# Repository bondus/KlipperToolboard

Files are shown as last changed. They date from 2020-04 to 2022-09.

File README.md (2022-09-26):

# Huvud 3D Printer toolhead board
A very small 3D printer board for use on a direct drive toolhead. It is designed to be used with Klipper firmware.
Klipper has the awesome feature to be able to use multiple MCUs connected to the host over a (relatively) high latency connection. Using CAN bus it is possible to chain many boards using just a pair of twisted wires and power. A good solution for multiple head 3D printers.

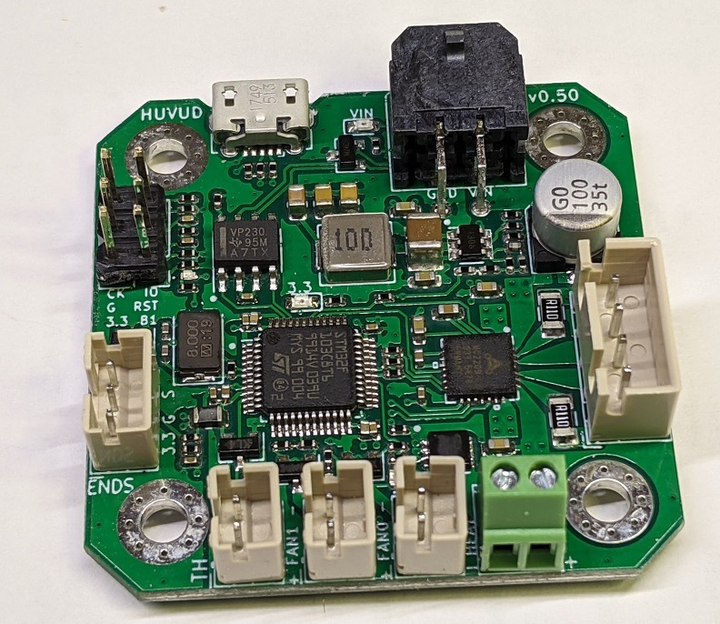
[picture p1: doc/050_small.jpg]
Image of Board


Features: 
* CAN bus. 
* One TMC2209 stepper driver for the extruder
* Two MOSFETs for fans
* One big MOSFET for the hotend heater
* Thermistor input
* Support for an endstop (or filament runout sensnor)
* STM32F103 72Mhz 32bit ARM MCU
* USB, for flashing firmware

Main power is 12-24V. 24V is preferred to keep the currents low

All done in KiCad and open source. 

If you are interesting in helping out, testing or eventually using this board feel free to contact me at glpontus@gmail.com.

### Documentation

* [Pinout and hook up](doc/pinout.md)
* [Klipper configuration](doc/klipper.md)
* [CAN bus](doc/canbus.md)
* [Prototype versions of the board](doc/versions.md)

---
Buy it at:

* Lukes Lab: https://lukeslabonline.com/products/huvud
* Tindie: https://www.tindie.com/products/huvud/huvud-3d-printer-hotend-control-board/

---

Read more about the project activites over at hackaday:
https://hackaday.io/project/174429-huvud-a-3d-printer-tool-head-controller-board

---

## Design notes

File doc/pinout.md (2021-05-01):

# Huvud Hardware, Pinout and Hookup

(all pictures are of pre production partially hand assembled boards, the real thing will be slighly different and look a lot better)

## Pinout 

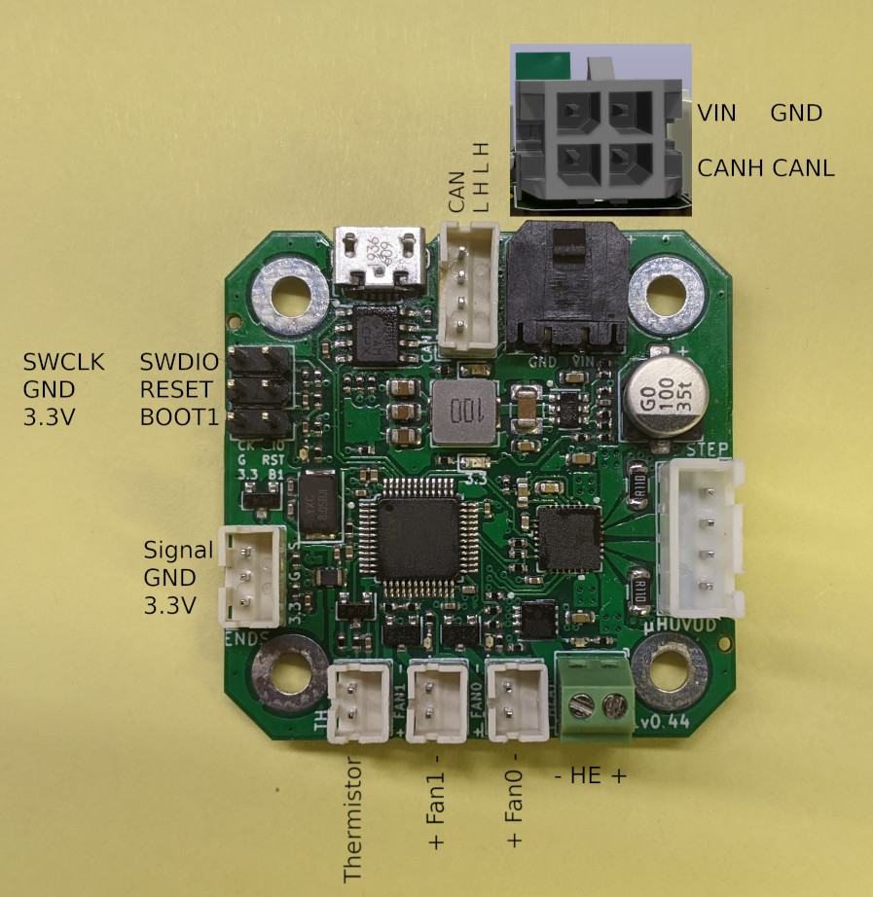
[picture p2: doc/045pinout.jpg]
Pinout


Function         | Pin  | Comment
-----------------|------|---------
Stepper EN       | PB6  |
Stepper STEP     | PB3  |
Stepper DIR      | PB4  |
Stepper DIAG     | PB5  |
Stepper Uart RX  | PA10 |
Stepper Uart TX  | PA9  |
CAN RX           | PB8  |
CAN TX           | PB9  |
USB +            | PA12 |
USB -            | PA11 |
FAN0             | PA8  |
FAN1             | PA7  |
Heater           | PA6  | 
Endstop          | PA1  | 10k pull up
Thermistor       | PA0  | 2.2k Pull Up
LED              | PC13 | Blue LED by the debug connector
Crystal 8Mhz     | PD0/PD1 |
BOOT1            | PB2  | 10k pull down
SWDIO            | PA13 | 10k pull down
SWDCLK           | PA14 | 10k pull down

Look at [printer.cfg](printer.cfg) for an example configuration.

## Powering

The board works from 10V up to 28V. It must be powered through the Molex Micro-Fit connector. It can not be powered with USB and powering though the 3.3V must be avoided, the stepper driver can get damaged.

The power connector is rated for max 8A

## Hooking up peripherals

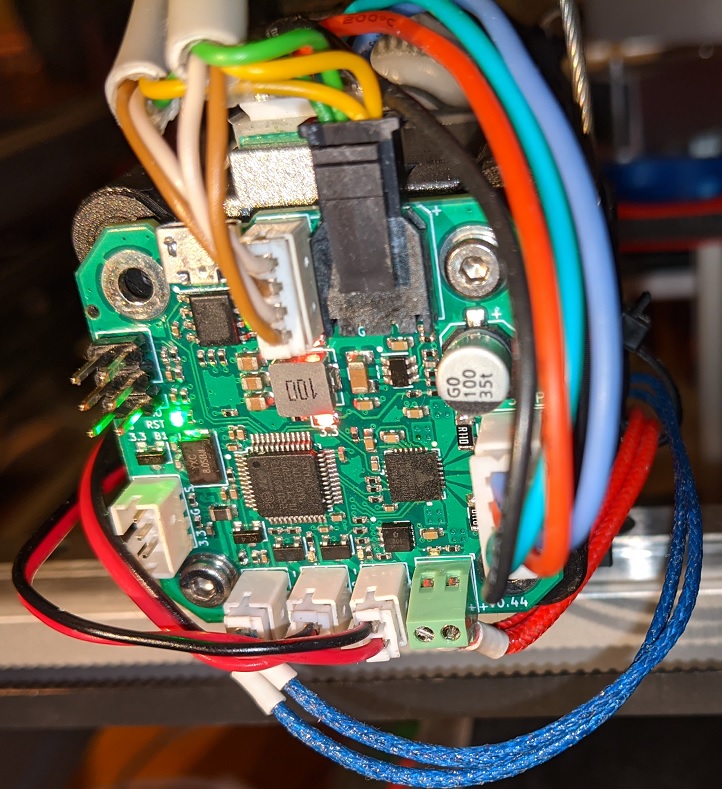
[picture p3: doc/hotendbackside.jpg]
Huvud on hotend


### Fans

JST-PH 2 mm connectors. Max 1A per fan

### Thermistor / PT1000

JST-PH 2 mm connectors. The thermistor input has a 2.2KOhm pullup resistor to allow for better resolution when using a PT1000 sensor.

### Hotend heater

Max 4A. Enough for a 100W heater when running on 24V

### Endstop

The endstop supplies 3.3V to work with an optical endstop sensors. For a microswitch (NO) connect it to GND and Signal.
Please note that klipper at the moment requires an endstop to be on the same board as the stepper driver. If the board is used for an extruder the endstop can not be used for a bed probe. The endstop can be used as a filament runout on a hotend, or as an axis endstop if the board is used for movement.

### CAN bus

Power and CAN bus in in the same Molex MicroFit connector.
There is no on board CAN bus termination resistor.

### LED

There is a user controlled green LED near the debug connector, it is connected to PC13. It is normally on while klipper is running. It's also used by the HID bootloader to signal various states.

## Thermals

The TMC2209 is a very efficient stepper driver and does not generate a large mount of heat. Still temerature should be checked if you run at high currents. The board is designed to spread the heat over the entire PCB. 

Testing shows that the board works comfortly without any extra cooling up to 1.2A driver current (it will reach about 25C above ambient). The board is designed to work up to 85C, so even if it gets very hot it will work fine. 

If the driver or boards gets too hot add small cooling fins, or if possible use a thick thermal pad on the bottom to lead the heat into something like an alu extrusion or other metal object.

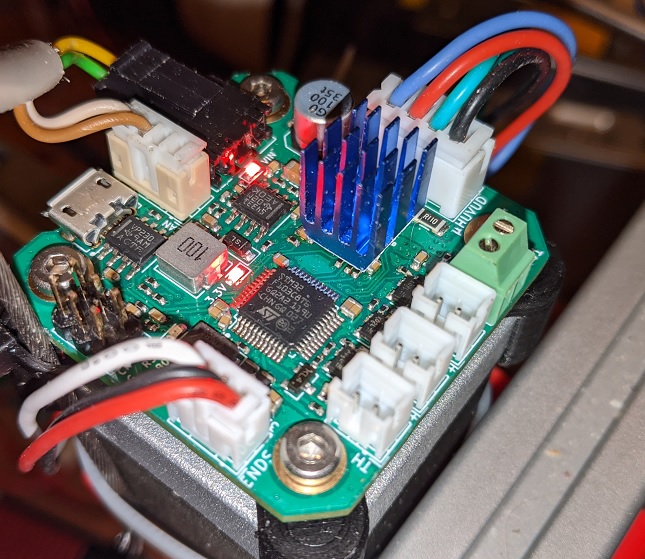
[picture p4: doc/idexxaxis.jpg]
IDEX x axis with cooling fins


If huvud is used for movement you can even monitor the temperature with a thermistor and turn on a fan if it gets too hot.

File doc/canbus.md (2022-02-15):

# Working with CAN bus

## Adapters

You will need a CAN bus adapter for your Raspberry Pi (or other board you run klippy on). There are many options available.

The adapter must support Linux socketcan

### USB CAN adapter

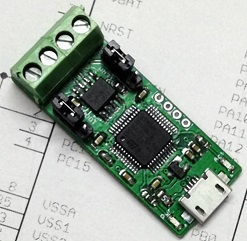
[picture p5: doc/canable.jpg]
Canable USB CAN clone


There is a very good open source firmware for STM32 based USB adapters, https://github.com/candle-usb/candleLight_fw. Any board running this firmware should work fine. There are plenty of open source hardware alteratives that runs this firmware.

Get one at https://openlightlabs.com/products/canable-0-4 or find a clone on aliexpress.

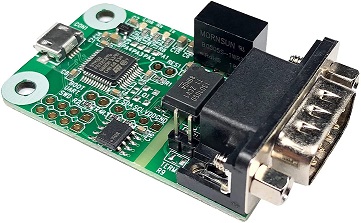
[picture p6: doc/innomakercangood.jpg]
Innomaker CAN USB


Innomaker has an USB CAN bus adapter widely available. It had a firmware bug that was reported and fixed March 2020, newer boards should have this fixed. 

### MCP2515 based CAN HATs

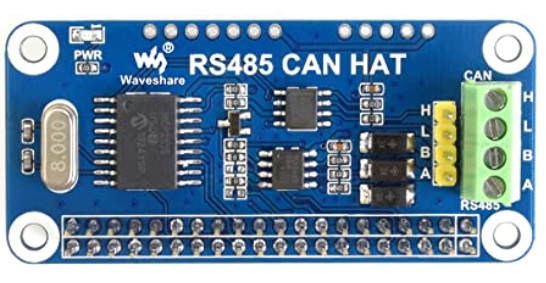
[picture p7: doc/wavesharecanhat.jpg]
Waveshare CAN HAT


The MCP2515 is a very common SPI connected CAN bus chip. It is a pretty bad options since it has very small buffers on chip and creates a lot of CPU load on the Raspberry Pi, and has a tendency to drop packet. It is not recomended if you use more than 1 or 2 boards or if you plan to use the accelerometer.

You have to run the CAN bus at 250kbits/s or possibly 500kbits/s. An older Pi, or a Pi Zero will not work reliably, it has to be a Pi3 or Pi4 or better.

An easily available option is "Waveshare RS485 CAN HAT"

TBD: Is the MCP2517/MCP2518 based HATs any better? They are made for CAN-fd but are backwards compatible. As the drivers are not in the mainline kernel it's non-trivial to get an MCP2517/8 to work. 

## Linux and Klipper setup

Please read https://github.com/KevinOConnor/klipper/blob/master/docs/CANBUS.md

## Wiring

### Cables

CAN bus is a bus, it must be terminated at each end with 120ohm resistors.

Twisted pair ... Ethernet cables or specifically made CAN bus cables. If shielding is used it should only be grounded at one point.

As we run default at 500kbits/s each stub length can be up to 1.6m long.

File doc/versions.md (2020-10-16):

# Versions of the Huvud Toolboard

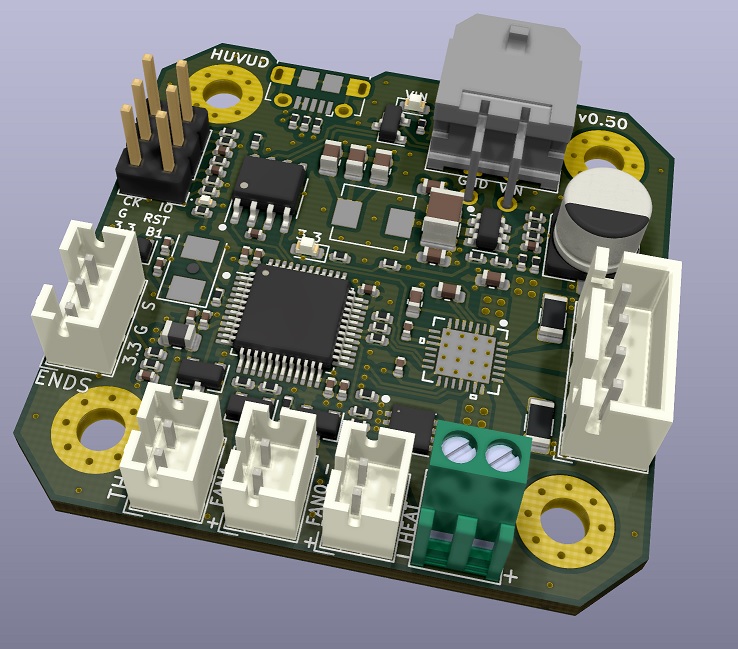
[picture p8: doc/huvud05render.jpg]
Render of Huvud v.050


## 0.50

Volume production about to start

+ Changed the power connector from a 2x1 Molex Micro-fit to a 2x2. The 2 extra pins are used for CAN bus. Allows one single connector back to klippy.
* Removed the 4 pin CAN connector
* Added ESD protection on the CAN bus
+ Test pads on the bottom for production testing

# Prototypes

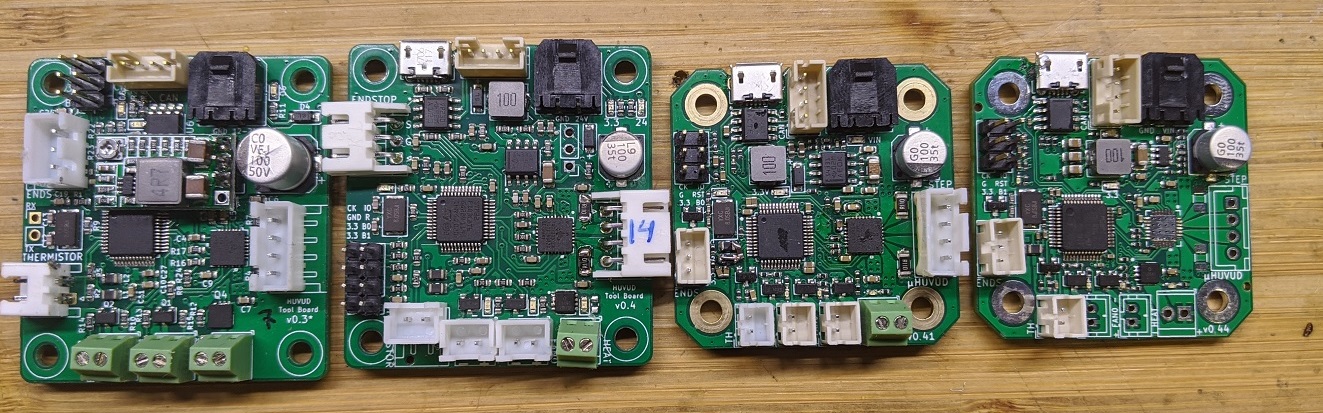
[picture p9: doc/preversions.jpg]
Pre production version


## 0.3

First Version

* 4.7k thermistor pullup
* 0.100ohm sense resistor for the TMC2209
+ It works!!!
- External 3.3V voltage regulator
- No USB, has to be flashed with an ST-LINK
- Very noisy thermistor signal (only seen when measuring, still works good in klipper)
* No SMDs smaller than 0603

## 0.4

+ USB
+ On board 3.3V voltage regulator 
+ 110ohm sense resistor

## 0.41

* 2.2k thermistor pullup to allow the use of PT1000 temperature proble
* Smaller size. 42x42 mm with 31x31 mm screw pattern, matches NEMA 17.
* Most small SMDs are 0402
* Most connectors changed to JST-PH 2.0 mm
* ESD protection on endstop and thermistor
- Weak heater MOSFET (max 4A with no margins at all)
- Forgot the pins for BOOT1, it's not possible to enter the bootloader

## 0.44

+ Greatly reduced ripple on 3.3V by redesigning and changing to a different voltage regulator IC
+ Greatly reduced thermistor noise, proper filtering of VREF

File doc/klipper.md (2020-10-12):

## Klipper configuration

### Firmware configuration

* Enable Micro-controller Architecture (STMicroelectronics STM32)
* Pick STM32F103
* Pick Bootloader offset (2KiB bootloader (HID Bootloader))
* Disable Use USB for communication (instead of serial)
* Enable Use CAN for communication (instead of seria)l
* Pick CAN pins (Pins PB8(rx) and PB9(tx))

It is possible to use USB instead of the CAN bus, like most other controller boards. 

### Bootloader and Flashing

The boards come preloaded with the HID bootloader for flashing over USB. Note that the board can not be powered over USB. 

To enter the bootloader pin BOOT1 must be connected to 3.3V when the board is powered up or reset. When in the bootloader the green LED will flash quickly. Flash with the command "make flash FLASH_DEVICE=1209:beba"

Hopefully a CAN capable bootloader will be developed to allow flashing over CAN bus.

### printer.cfg

[Example partial printer.cfg](printer.cfg)

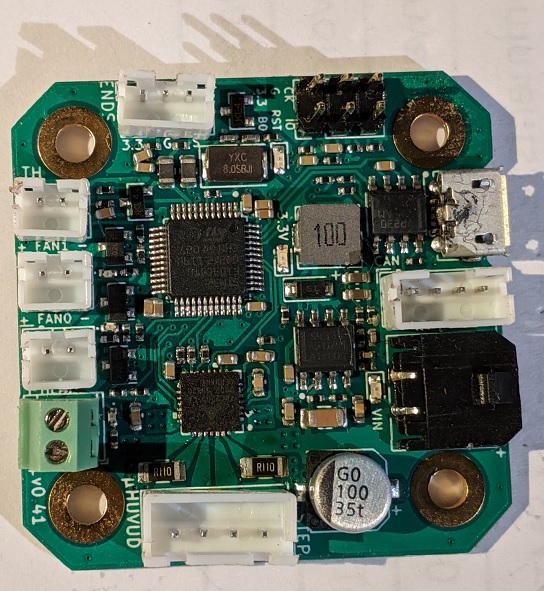
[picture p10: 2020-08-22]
doc/uHuvud0.41.jpg

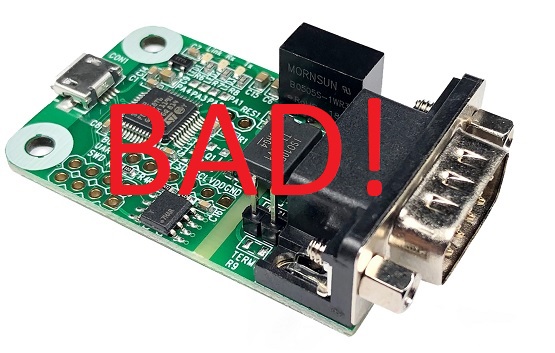
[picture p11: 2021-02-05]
doc/innomakerusbcan.jpg

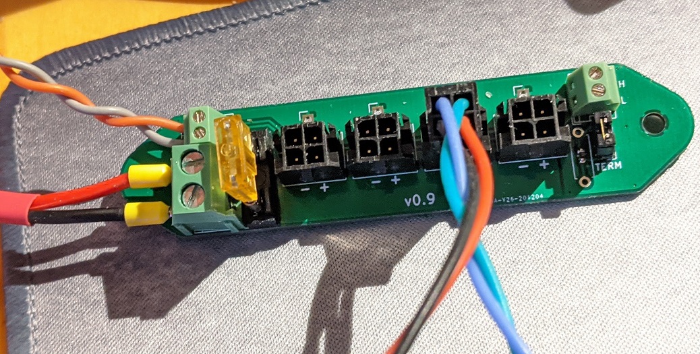
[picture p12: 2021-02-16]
doc/PowerCanDist.jpg

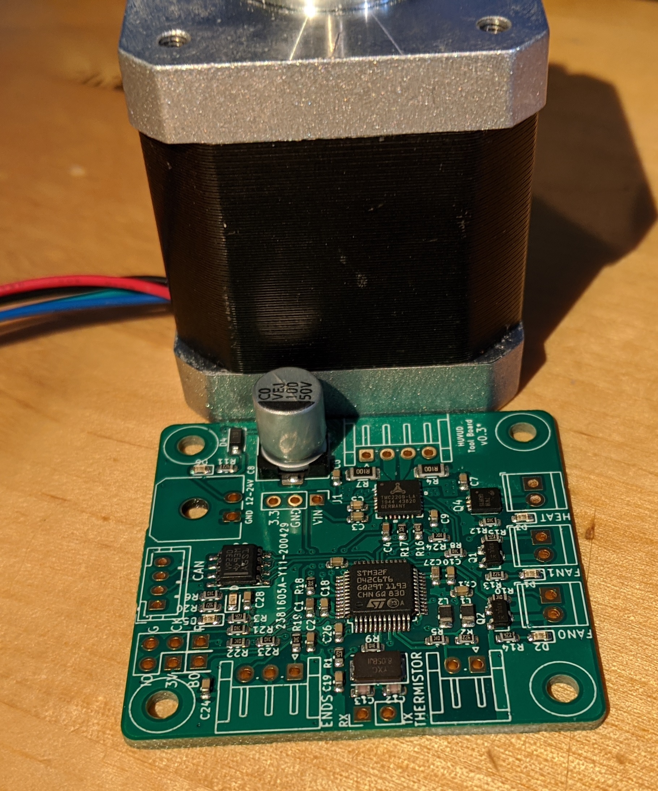
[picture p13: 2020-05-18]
FirstPic.jpg

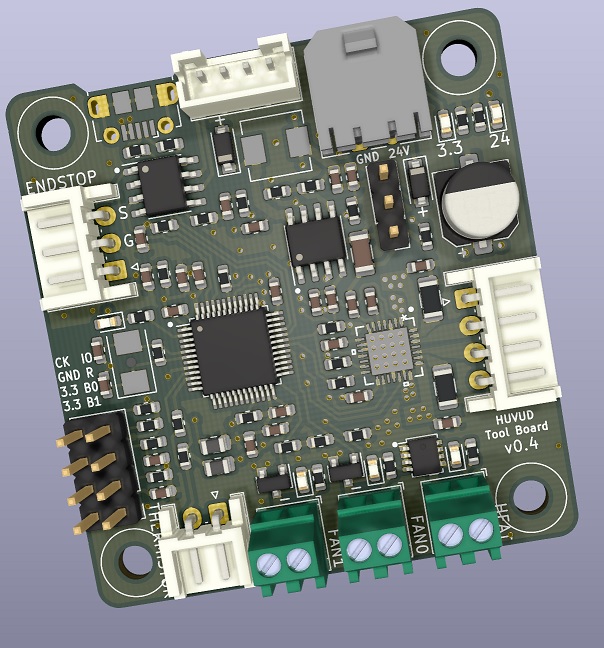
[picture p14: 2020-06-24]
doc/Huvud0.4Render.jpg

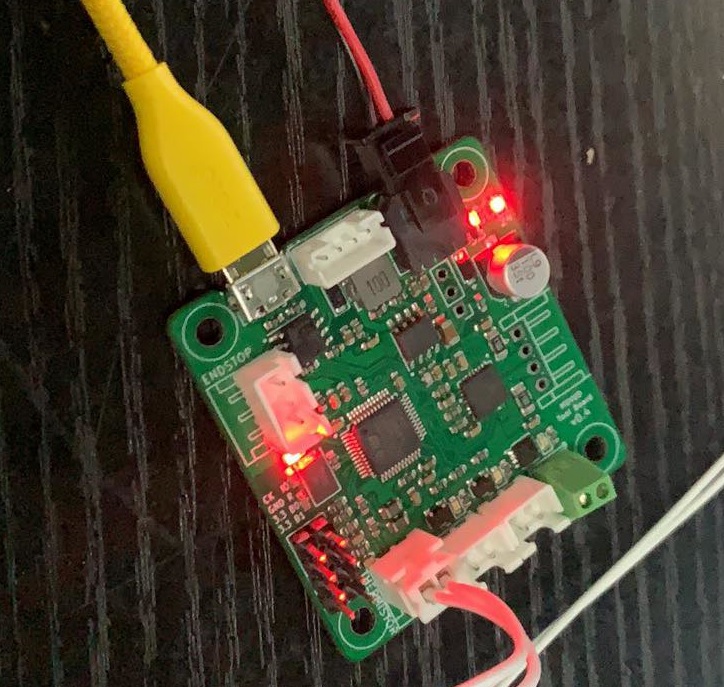
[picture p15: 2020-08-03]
doc/Huvud0.4Real.jpg

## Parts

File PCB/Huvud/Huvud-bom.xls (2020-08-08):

Item # | Designator | Qty | Manufacturer | Part Nr | Value | Package | Type | Notes | LCSC Part #（optional）
1 | C11,C10,C17,C18,C19,C26,C28,C2,C24,C21 | 10 |  |  | 0.1uF | 0603 | SMD |  | C14663
2 | C12,C13 | 2 |  |  | 22pF | 0603 | SMD |  | C1653
3 | C14 | 1 |  |  | 2.2nF | 0603 | SMD |  | C1604
4 | C15 | 1 |  |  | 15pF | 0603 | SMD |  | C1644
5 | C16 | 1 |  |  | 10nF | 0603 | SMD |  | C57112
6 | C20 | 1 |  |  | 10uF | 1206 | SMD |  | C13585
7 | C22,C23 | 2 |  |  | 10uF | 0603 | SMD |  | C19702
8 | C4,C1,C27 | 3 |  |  | 4.7uF | 0603 | SMD |  | C19666
9 | C5 | 1 |  |  | 22nf/50V | 0603 | SMD | Min 35V | C21122
10 | C8 | 1 | Lelon | VZT101M1VTR-0606 | 100uF/35V | CP_Elec 6.3x5.8 | SMD | Min 35V | C249982
11 | C9,C6,C7,C3 | 4 |  |  | 100nF/50V | 0603 | SMD | Min 35V | C14663
12 | D1,D3,D2 | 3 |  |  | LED Green | 0603 | SMD |  | C72043
13 | D4,D7 | 2 | Changjiang Electronics Tech | B5819W | B5819W | SOD-123 | SMD |  | C8598
14 | D6,D8,D5 | 3 |  |  | LED Red | 0603 | SMD |  | C2286
15 | J12 | 1 | Molex | 105017-0001 | USB_Micro-B_Molex-105017-0001 | USB_Micro-B_Molex-105017-0001 | SMD |  | C10418
16 | L1,L2 | 2 |  |  | 22uH | 0805 | SMD |  | C32375
17 | L3 | 1 | Sunlord (or similar) | MWSA0503-100MT | 10uH | 5.2x5.4x3.0mm | SMD |  | C139506
18 | Q2,Q1 | 2 | Alpha & Omega Semicon (or similar) | AO3400A | AO3400A | SOT-23 | SMD |  | C20917
19 | Q4 | 1 | Shenzhen ruichips Semicon | RU3040M2 | RU3040M2 | PDFN3333 | SMD | Dot on silk matches dot on chip | C180958
20 | R18,R17,R24 | 3 |  |  | 20k | 0603 | SMD |  | C4184
21 | R2,R1 | 2 |  |  | 4.7k | 0603 | SMD |  | C23162
22 | R20,R3 | 2 |  |  | 470 | 0603 | SMD |  | C23179
23 | R25,R26 | 2 |  |  | 20 | 0603 | SMD |  | C22950
24 | R27 | 1 |  |  | 1.5k | 0603 | SMD |  | C22843
25 | R29 | 1 |  |  | 18k | 0603 | SMD |  | C25810
26 | R31 | 1 |  |  | 3.3k | 0603 | SMD |  | C22978
27 | R32 | 1 |  |  | 160k | 0603 | SMD |  | C22813
28 | R33 | 1 |  |  | 30k | 0603 | SMD |  | C22984
29 | R4,R7 | 2 | 1% 1/4W |  | 0.11 | 1206 | SMD |  | C247458 (https://lcsc.com/product-detail/Low-Resistors-Current-Sense-Resistors-Surface-Mount_Uniroyal-Elec-1206W4J011KT5E_C247458.html/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)
30 | R5,R8,R13,R10,R12,R15,R14,R11,R23,R19,R21,R22,R28,R30 | 14 |  |  | 10k | 0603 | SMD |  | C25804
31 | R6,R16 | 2 |  |  | 1k | 0603 | SMD |  | C21190
32 | R9 | 1 |  |  | 1M | 0603 | SMD |  | C22935
33 | U1 | 1 | Texas Instruments | TPS54331DR | TPS54331DR | SOIC-8 3.9x4.9mm_P1.27mm | SMD | Dot on silk matches dot on chip | C9865
34 | U2 | 1 | TRINAMIC Motion Control GmbH | TMC2209-LA | TMC2209-LA | TMC2209:TMC2209-LA | SMD | Dot on silk matches dot on chip | C465949
35 | U5 | 1 | ST Microelectronics | STM32F103C8T6 | STM32F103C8T6 | LQFP-48 7x7mm_P0.5mm | SMD | Dot on silk matches dot on chip | C8734
36 | U6 | 1 | Texas Instruments | SN65HVD230 | SN65HVD230 | SOIC-8 3.9x4.9mm_P1.27mm | SMD | Dot on silk matches dot on chip | C12084
37 | Y1 | 1 | Yangxing Tech (or similar) | X50328MSB2GI | 8Mhz | 5032 2Pin_5.0x3.2mm | SMD |  | C115962
 |  | 80
 | Ignore below
 | J1 |  |  |  | PinHeader_1x3_P2.54mm | Connector_PinHeader_2.54mm:PinHeader_1x03_P2.54mm_Vertical
 | J10 |  |  |  | JST_PH_1x04_P2.00mm_Vertical | Connector_JST:JST_PH_B4B-PH-K_1x04_P2.00mm_Vertical |  |  | C265289
 | J2 |  |  |  | PinHeader_2x4_P2.54mm | Connector_PinHeader_2.54mm:PinHeader_2x04_P2.54mm_Vertical
 | J3 |  |  |  | JST_EH_1x2_P2.50mm_Horizontal | Connector_JST:JST_EH_S2B-EH_1x02_P2.50mm_Horizontal |  |  | C132479
 | J4 |  |  |  | FAN0 | Huvud:TerminalBlock_TE_282834-2_1x02_P2.54mm_Horizontal |  |  | C557685
 | J5 |  |  |  | FAN1 | Huvud:TerminalBlock_TE_282834-2_1x02_P2.54mm_Horizontal |  |  | C557685
 | J6 |  |  |  | Heater | Huvud:TerminalBlock_TE_282834-2_1x02_P2.54mm_Horizontal |  |  | C557685
 | J7 |  |  |  | JST_EH_1x3_P2.50mm_Horizontal | Connector_JST:JST_EH_S3B-EH_1x03_P2.50mm_Horizontal |  |  | C168980
 | J9 |  |  |  | JST_EH_1x4_P2.50mm_Horizontal | Connector_JST:JST_EH_S4B-EH_1x04_P2.50mm_Horizontal |  |  | C132474
 | J8 |  | Molex | Micro-Fit 3.0 43650-0200 | Conn_01x02 | Connector_Molex:Molex_Micro-Fit_3.0_43650-0200_1x02_P3.00mm_Horizontal |  |  | C239446

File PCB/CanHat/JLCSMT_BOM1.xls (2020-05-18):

Comment | Designator | Footprint | LCSC Part #（optional）
22p | C1 C2 | 0603 | C1653
1k | R1 | 0603 | C21190
10k | R2 | 0603 | C25804
120R | R3 R4 R5 R6 R7 | 0603 | C22787
MCP2515-xSO | U1 | SOIC-18W_7.5x11.6mm_P1.27mm | C12368
SN65HVD230 | U2 | SO:SOIC-8_3.9x4.9mm_P1.27mm | C12084
Crystal | Y1 | SMD 5032-2Pin_5.0x3.2mm | C115962

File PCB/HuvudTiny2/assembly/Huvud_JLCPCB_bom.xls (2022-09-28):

Comment | Designator | Footprint | JLCPCB Part #（optional）
4.7uF | C1,C4,C23,C27,C33,C35,C41 | Capacitor_SMD:C_0402_1005Metric | C23733
22pF | C12,C13,C26,C29 | Capacitor_SMD:C_0402_1005Metric | C1555
22uF | C14,C15,C32 | Capacitor_SMD:C_0805_2012Metric | C602037
0.1uF | C2,C9,C10,C11,C17,C18,C19,C24,C25,C28,C30,C31,C34,C36,C42 | Capacitor_SMD:C_0402_1005Metric | C1525
68pF | C21 | Capacitor_SMD:C_0402_1005Metric | C14441
10uF/35V | C22 | Capacitor_SMD:C_1210_3225Metric | C13585
0.1uF/35V | C3,C6,C7,C16,C20 | Capacitor_SMD:C_0603_1608Metric | C14663
470pF/100V | C37,C38,C39,C40 | Capacitor_SMD:C_0603_1608Metric | C107062
22nf/50V | C5 | Capacitor_SMD:C_0603_1608Metric | C21122
100uF/35V | C8 | Capacitor_SMD:CP_Elec_6.3x5.8 | C249982
LEDGR | D1,D2,D3,D5 | LED_SMD:LED_0402_1005Metric | C74338
LEDRED | D6,D8 | LED_SMD:LED_0603_1608Metric | C2286
SM24CANB | D7 | Package_TO_SOT_SMD:SOT-23 | C970029
Conn_02x02_Odd_Even | J1 | Connector_Molex:Molex_Micro-Fit_3.0_43045-0400_2x02_P3.00mm_Horizontal | C122413
USB_Micro-B_Molex-105017-0001 | J12 | Connector_USB:USB_Micro-B_Molex-105017-0001 | C10418
DBG | J2 | Connector_PinHeader_2.54mm:PinHeader_2x03_P2.54mm_Vertical | C65114
THERM | J3 | Connector_JST:JST_PH_B3B-PH-K_1x03_P2.00mm_Vertical | C2320
FAN0 | J4 | Connector_JST:JST_PH_B2B-PH-K_1x02_P2.00mm_Vertical | C2319
FAN1 | J5 | Connector_JST:JST_PH_B2B-PH-K_1x02_P2.00mm_Vertical | C2319
Heater | J6 | Huvud:TerminalBlock_TE_282834-2_1x02_P2.54mm_Horizontal | C557685
Endstop | J7 | Connector_JST:JST_PH_B5B-PH-K_1x05_P2.00mm_Vertical | C2322
STEPPER | J9 | Connector_JST:JST_XH_B4B-XH-A_1x04_P2.50mm_Vertical | C144395
Jumper | JP3 | Connector_PinHeader_2.00mm:PinHeader_1x02_P2.00mm_Vertical | C376075
22uH | L1 | Inductor_SMD:L_0805_2012Metric | C32375
10uH/max 145mOhm 2A | L4 | Inductor_SMD:L_Sunlord_MWSA0518_5.4x5.2mm | C408412
AO3400A | Q1,Q2 | Package_TO_SOT_SMD:SOT-23 | C20917
JSM7788 | Q3 | Huvud:DFN-8-1EP_3x3mm_P0.65mm_EP1.7x2.05mm | C2874722
10k | R1,R5,R8,R10,R11,R12,R13,R14,R15,R19,R21,R22,R23,R30,R32,R33,R36,R37,R42,R43 | Resistor_SMD:R_0402_1005Metric | C25744
22k | R17,R18,R24,R39 | Resistor_SMD:R_0402_1005Metric | C25768
2.2k 0.1% | R2,R31 | Resistor_SMD:R_0402_1005Metric | C445604
22 | R25,R26,R28,R34,R35 | Resistor_SMD:R_0402_1005Metric | C25092
2.2k | R27,R29 | Resistor_SMD:R_0402_1005Metric | C25879
470 | R3,R20 | Resistor_SMD:R_0402_1005Metric | C25117
120 100mW | R38 | Resistor_SMD:R_0603_1608Metric | C22787
0.110 1% | R4,R7 | Resistor_SMD:R_1206_3216Metric | C25334
100k | R40 | Resistor_SMD:R_0402_1005Metric | C25741
13.7k | R41 | Resistor_SMD:R_0402_1005Metric | C25854
1k | R6,R16 | Resistor_SMD:R_0402_1005Metric | C11702
1M | R9 | Resistor_SMD:R_0402_1005Metric | C26083
ADXL345 | U1 | Package_LGA:LGA-14_3x5mm_P0.8mm_LayoutBorder1x6y | C9667
TMC2209-LA | U2 | TMC2209:TMC2209-LA | C465949
TPS54202 | U3 | Package_TO_SOT_SMD:SOT-23-6 | C191884
XC6206PxxxMR | U4 | Package_TO_SOT_SMD:SOT-23 | C5446
STM32F103C8T6 | U5 | Package_QFP:LQFP-48_7x7mm_P0.5mm | C8734
SN65HVD230 | U6 | Package_SO:SOIC-8_3.9x4.9mm_P1.27mm | C12084
8Mhz | Y1 | Crystal:Crystal_SMD_5032-2Pin_5.0x3.2mm | C115962

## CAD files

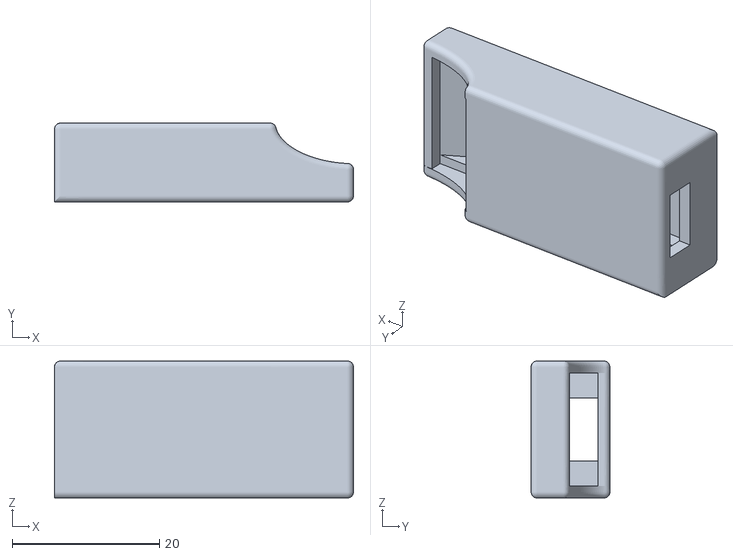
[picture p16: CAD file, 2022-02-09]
PCB/HuvudCanUSB/USBCANCase.stl
40.6 x 10.7 x 18.6

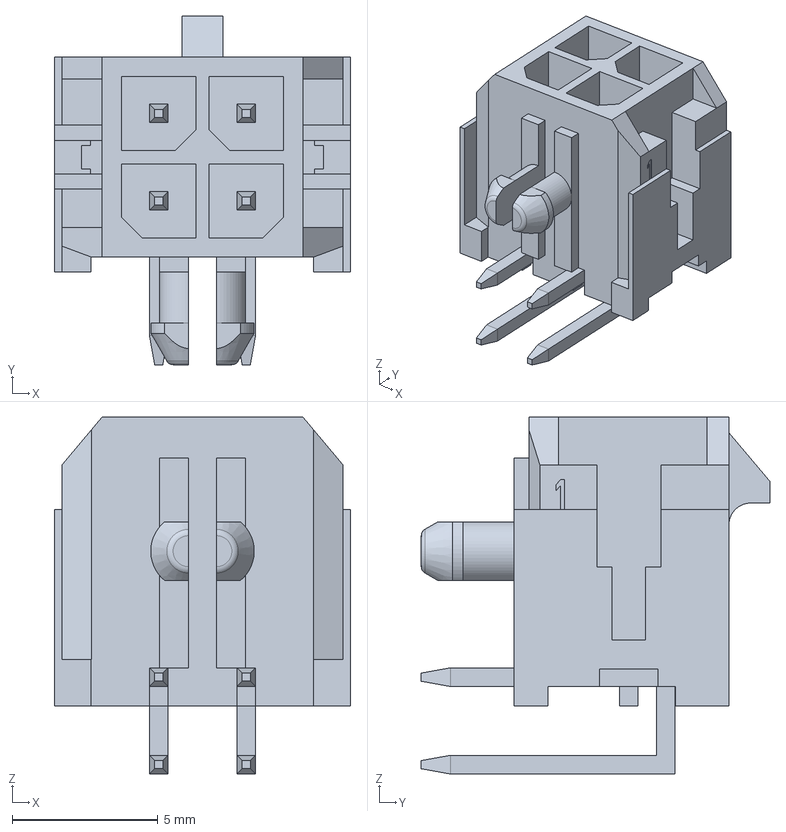
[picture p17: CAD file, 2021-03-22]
PCB/HuvudTiny2/3D/molex_430450400.stp
10.1 x 12.0 x 12.2 mm

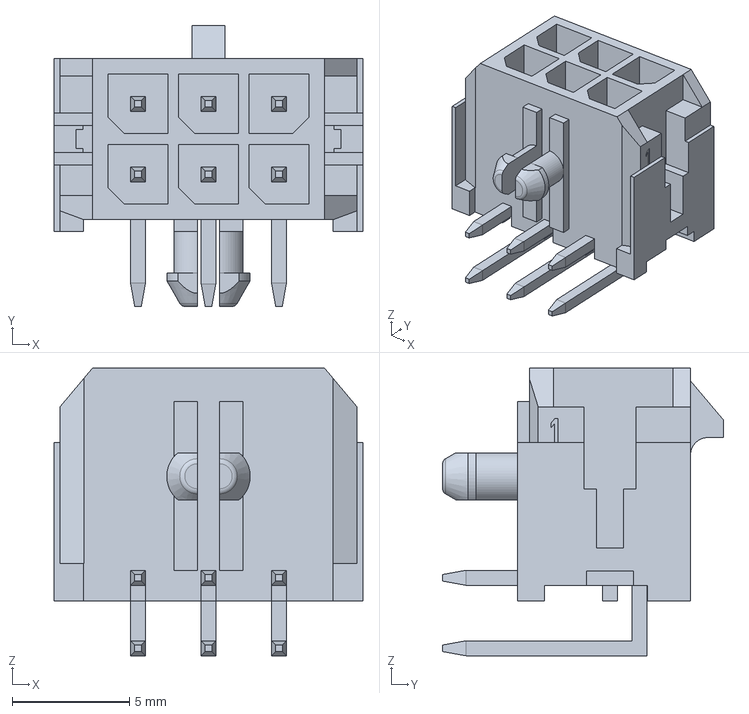
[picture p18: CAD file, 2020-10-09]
PCB/HuvudTiny2/3D/molex_430450600.stp
13.2 x 12.0 x 12.2 mm

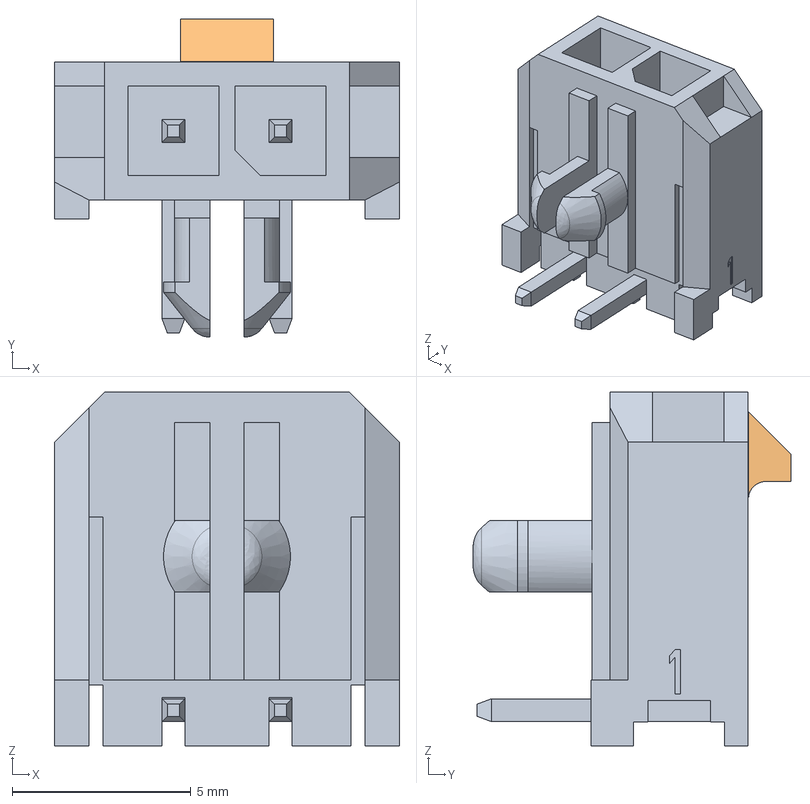
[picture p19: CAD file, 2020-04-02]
PCB/HuvudTiny2/3D/molex_436500200.stp
9.65 x 8.90 x 9.90 mm

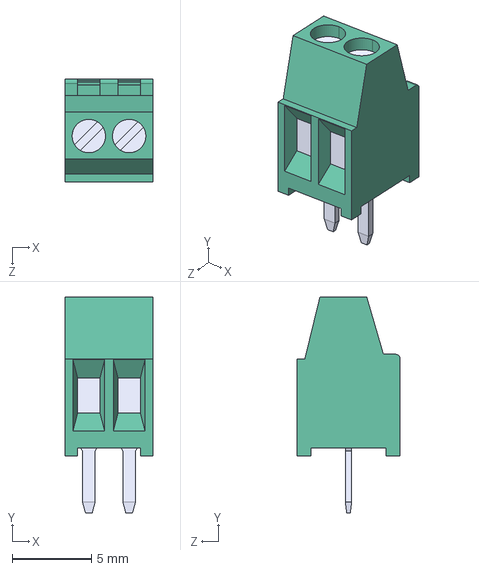
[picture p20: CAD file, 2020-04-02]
PCB/HuvudTiny2/3D/TE_282834-2--3DModel-STEP-56544.STEP
5.54 x 13.6 x 6.50 mm

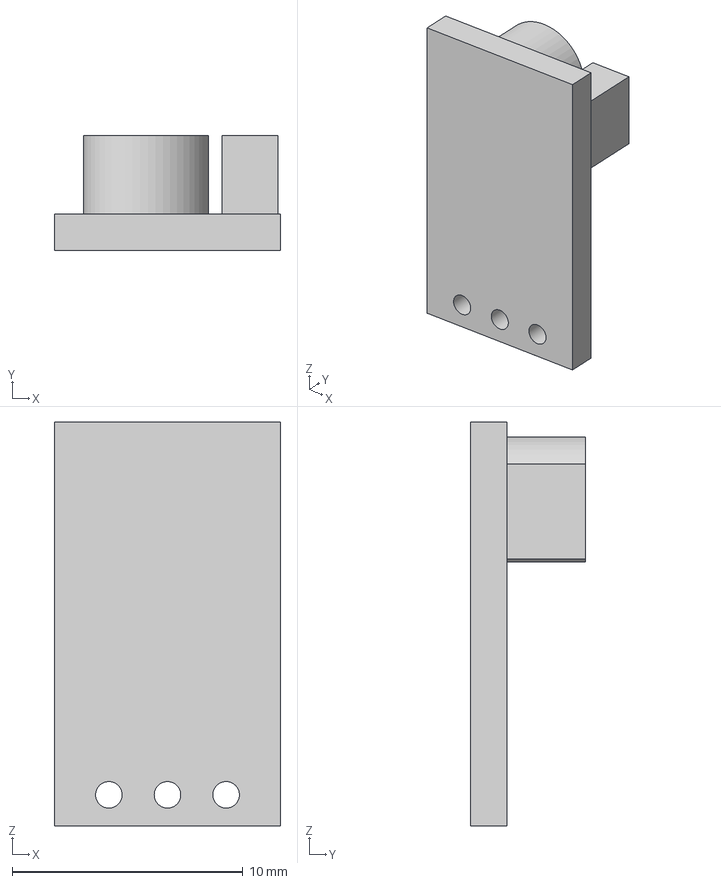
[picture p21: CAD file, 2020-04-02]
PCB/HuvudTiny2/3D/Regulator.step
9.80 x 5.00 x 17.5 mm

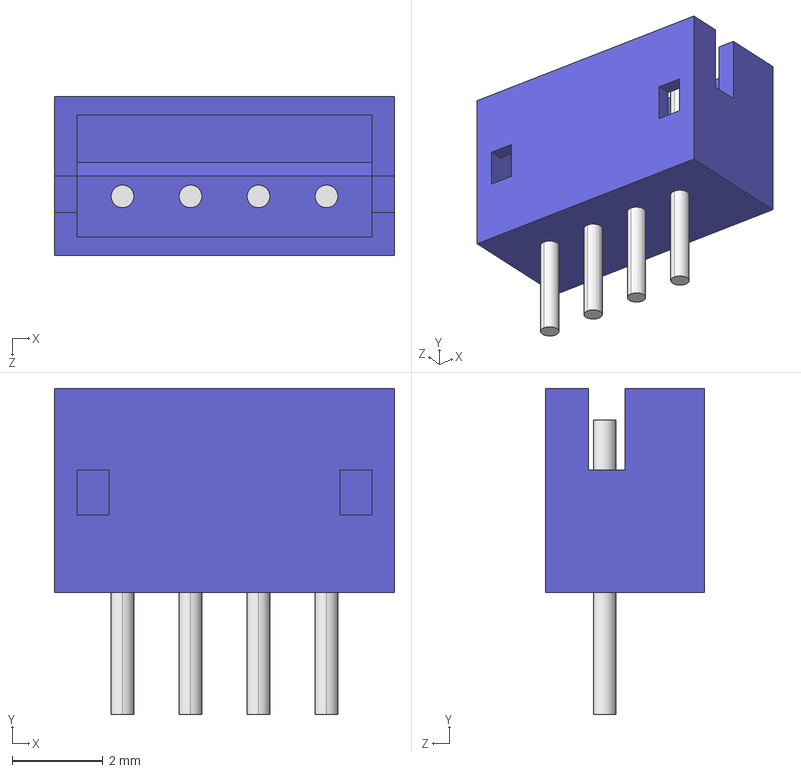
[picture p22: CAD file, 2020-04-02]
PCB/HuvudTiny2/3D/B4B-ZR.STEP
7.50 x 7.20 x 3.50 mm

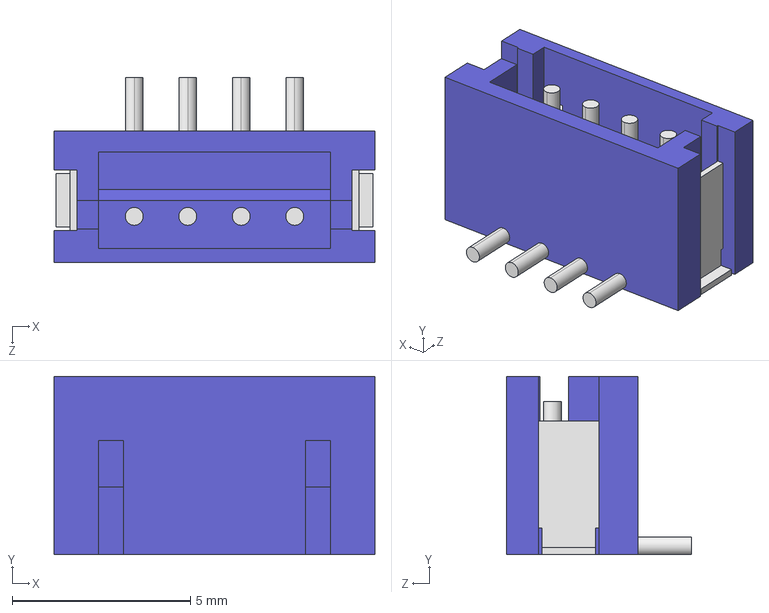
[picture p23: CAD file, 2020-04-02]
PCB/HuvudTiny2/3D/B4B-ZR-SM4-TF.STEP
9.00 x 5.00 x 5.20 mm

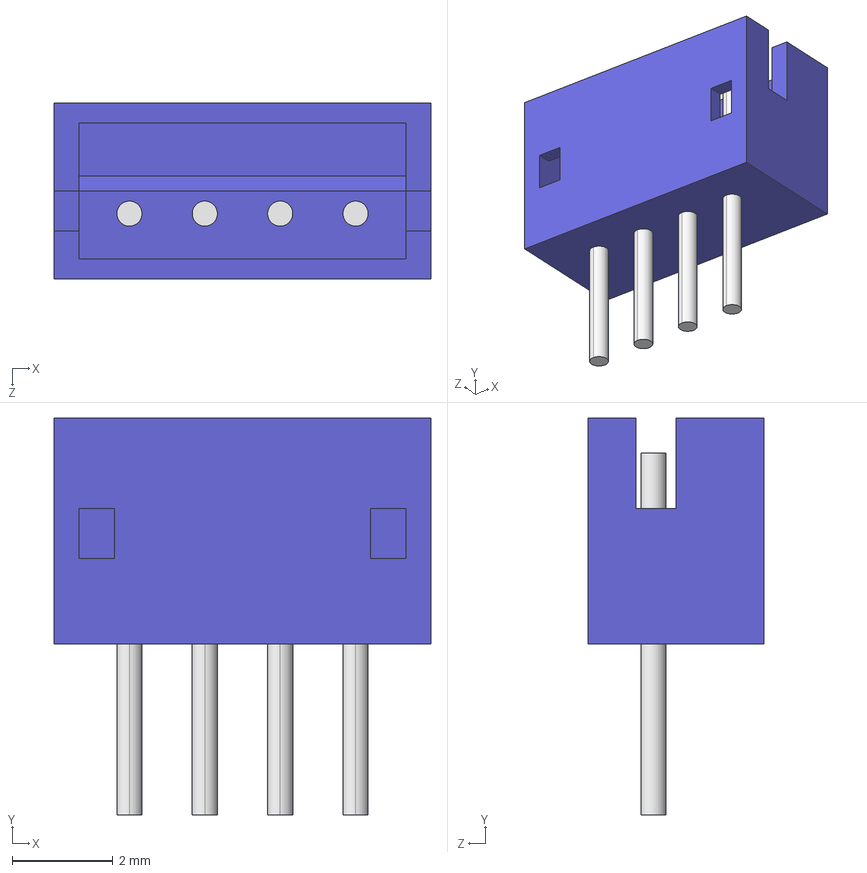
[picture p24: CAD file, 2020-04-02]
PCB/HuvudTiny2/3D/B4B-ZR-3.4.STEP
7.50 x 7.90 x 3.50 mm

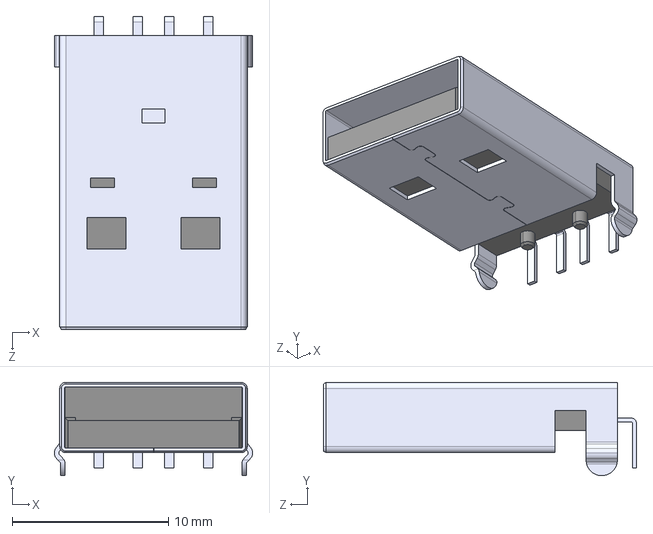
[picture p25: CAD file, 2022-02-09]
PCB/HuvudCanUSB/Molex/48037-0001.step
12.7 x 5.97 x 20.0 mm

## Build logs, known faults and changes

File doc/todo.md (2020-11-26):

# Things to do and random ideas

## Hardware Change Ideas

* Connectors for I2C,SPI,neopixel ...
  * Could double as a connector for a small daughterboard
* Fine pitch connector for the debug connector
* Tiny buttons for rst/boot1 ...
* On board g-force/gyro chip, or as a small daughterboard
* Change to a 5V DCDC and a linear 3.3V?  To provice 5V for things like LEDs and servos.

### Software

* Develop a CAN bus capable bootloader for flashing over CAN. Probably needs incompatible changes to the CAN protocol
* Improve the CAN bus protocol to be more bandwidth efficient. Such as rely on CAN CRC and remove klipper CRC
* Modify klipper firmware to keep USB usable when using CAN bus
 * At least allow USB to detect boot loader trying to flash
 * Automatic switching to/from USB when connected

#### Bugs/flaws

* It's not possible to enter DFU bootloader when in klipper firmware automatically. The SWD pins might be in the wrong state.
* The CanSerial utility/Linux CAN bus interface is not as stable as you might wish

### Hardware issues

* The TPS54308 DCDC converter generates a lot of heat at idle. Is there a better way to get 3.3V with low ripple?

## Hardware Cost Cutting

* Use an STM32F0
 * no crystal needed? Even for CAN?
* Change to some cheap generic DCDC controller.

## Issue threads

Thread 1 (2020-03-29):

Add connector labels

RaymondHimle, 2020-03-29:
It might be early on but adding silkscreen labels for the intended use of all the connectors would be helpful.

bondus, 2020-06-09:
Indeed. I'm trying to keep them as marked as possible all the time now. It's tricky to find space for it.

Closed 2020-06-09.

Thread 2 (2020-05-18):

JLCSMT_Sample_BOM1

Tiefschneegiftler, 2020-05-18:
LCSC Part C21190, the UNIROYAL 1k resistor is in there twice once in line 17 once in 18, with Designators R4 and R6 respectively, shouldn't they go into one line?
I think you have the description with a capital K in the one and the non cap k in the other so the automated BOM put it into two lines.

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

bondus, 2020-05-18:
You are right. But that BOM is very obsolete. The git was just now updated to the recent version.

Closed 2020-05-18.

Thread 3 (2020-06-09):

Can hat power back feed?

trevjonez, 2020-06-09:
Wanted to ask if you have considered adding a 24 to 5v regulator to the can hat possibly with two jumpers (one positive, one negative) which would feed 5v back into the pi to power it. thus eliminating the need for the micro usb or usb c cable to power the pi. Jumpers so it could be easily disabled or bypassed if that made sense for a given application.

Just thinking aloud as I am running pi 3b+ on my machines and utilize a small buck converter on the gpio pins (04,06) for power. Given the hat design photographed I would need to change some of my setup should I ever try to utilize a setup on par with what you have demonstrated here. but eliminating the extra dangling buck converter would be a nice to have.

bondus, 2020-06-10:
I have been thinking the exact same thoughts, the current CAN hat is a quick hack.
There is a new versions of the hat in the works with (among other features) pins to solder an external buck converter. But I am still looking for a good, cheap, small, easily available 5V 3A converter that can do the job. The Pi is very picky on power delivery.

trevjonez, 2020-06-10:
I don't have hardware knowledge beyond the very basics but I have had a good experience with these cheap buck converters thus far. https://www.amazon.com/gp/product/B07RVG34WR

A point of friction with those is that you need a dmm you trust to adjust the voltage before attaching to the PI. [Somewhere on the internet it told me](https://magpi.raspberrypi.org/articles/power-supply) to be careful about voltage when powering via the GPIO pins since there is not a fuse or regulator through that path. I've no clue if that little buck is risking the 3b+'s life though i've yet to have an issue and generally trust my meanwell 24v supply's

what is the motivation for using an external part for power conversion vs adding it directly to the hat pcb?

Closed 2020-06-11.

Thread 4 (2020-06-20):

Cannot Find a way to contact, author

SteveJWallace, 2020-06-20:
There is no email or other way to contact the author.

bondus, 2020-06-24:
You found a way. It's improved now

SteveJWallace, 2020-06-24:
Hey, I was trying to reach out to you. I'm currently building a Jubilee
toolchanger and implementing it using 2. SKR Pro 1.1 boards and klipper.
Most Jubilee printers currently are built with duet2/3 and tool boards. A
future project was to build a tool board but someone pointed me in your
direction.

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

bondus, 2020-06-25:
Klipper screamed to get a board like this, the design of klipper makes it very easy. A multi head printer needs a product like this.
I'm stuck in a horrible world of SMT assembly and manufacture at the moment. With some luck there will be some working boards for sale at the end of the summer.

SteveJWallace, 2020-06-25:
If you want any testers etc, I'm quite technical. I'm not a professional EE
by any means but have worked in embedded systems as a software developer
and electronics hobbyist.

My only issue with klipper is that it's uses a serial protocol that isn't
really best served over Can.

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

bondus, 2020-06-25:
Where are all the EEs when you need them? Hidden in some corporate basement!
The current CAN implementation tunnels serial over CAN, far from ideal but it gets the job done. Each board gets its own virtual serial port.  Not very different from how USB serial does it.
We could make a better implementation that integrates better with how the klipper serial protocol works. But it works as is, I can't see any major issues with it. It currently has a separate daemon that does the CAN work (https://github.com/Delsian/CanSerial) that could be a part of klippy.
Klipper is very light on serial use and is quite latency and error tolerant. Each board uses peek ~30 kbits/s. I can easily run all my 5 prototypes on one 500kbit/s bus. I estimate that for a stable system you should not use more than 8 per 500kbit/s CAN bus. But you can have many busses per host (The CAN hats for the PI's are horrible for scaling, it's better to use USB dongles).
CAN, being a bus, makes it possible to sniff, analyze and inject traffic on the bus. As it is a strict priority bus it's easy to fill it to 75% with high prio junk trafic, or flood it with low prio traffic. I have had a lot of fun :)

SteveJWallace, 2020-06-25:
The main issue I see is that the serial protocol itself doesn't fit can
well. As an example, typically in can, collisions are detectable and less
significant bits succeed atop higher bit commands. This means that cmd will
always be heard. This is commonly used in embedded systems as a hard stop
for everything.

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

SteveJWallace, 2020-06-25:
Anyhow, if I can be of any use let me know. My c/c++ is rusty as heck. But
I have lots of experience in troubleshooting rs-485 and Can.

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

Closed 2020-06-24.

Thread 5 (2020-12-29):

Higher Voltage version

bung69, 2020-12-29:
Hi,

Really like this project.

Do you think it would be feasible to support a wider range of voltages,  up to 48V or 60V  for use with large machines and motors?

raymondh2, 2020-12-30:
48 or 60 volt would require a different stepper driver. It would also likely require changes to other power circuitry.

bondus, 2020-12-30:
The stepper driver used, TMC2209, is limited to 29V. Higher voltage drivers require external mosfets which require more space.
And the power components would have to be totally different as ray writes, below 35V you have a plethora of options.
Higher voltages do require special care to avoid sparks and such that I know nothing about.

olinek2, 2021-01-18:
You can use https://www.trinamic.com/products/integrated-circuits/details/tmc261c-pa/
I am running it at 50 VDC without any problems :)

Mosher23, 2021-04-18:
TMC5160 can run up to 50V, so 48V would be really nice for CoreXY printers for X-Y Movements

theolas, 2022-03-11:
> TMC5160 can run up to 50V, so 48V would be really nice for CoreXY printers for X-Y Movements

As bondus said, those require external mosfets that take up more space.

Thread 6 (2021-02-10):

BL/Touch support

jstkatz, 2021-02-10:
Its a good concept, for my particular use being able to add a bl touch in addition to an endstop would be useful, the touch could remove an additional 2-4 wires though it does require being able to supply 300ma at 5V briefly

Along the same lines, support for an inductive probe might instead of the touch would likely be preferred by some, because they're unlikely to both be used you might be able to save some space by overlapping the header footprints or selecting the supply voltage pin as either 5 or Vin via a solder jumper

bondus, 2021-02-10:
When the board was designed klipper had no support for a probe or endstop on the MCU running the extruder, so endstops were very low priority. Now work is being done in klipper to allow that, it'll hopefully be finished soon.
For the next version I'll try to squeeze in 5V and certainly more and better endstop/probe support.

mraction, 2021-07-18:
In the current state of the V0.6, you can use BL-Touch, if you don't solder R19 und C2 and short R36. Then you can use Pin 3 from the J7 Connector for the Control-Pin from your BL-Touch.

Connect the sensor Pin from the BL Touch to Pin2 or Pin1 from the J7 Connector and how to connect 5V and GND should be clear. ;-)

Alternativ it should be possbile to use SWCLK or SWDIO from the debug port for the Control-Pin from the BL-Touch?

bondus, 2021-07-21:
Thanks for the hints. Looking at he BL-Touch docs it looks like all that is needed is a raw output PWM capable pin from the MCU, it will work with 3.3V for that PWM signal.
I have considered moving the debug connector to pads on the back, they aren't really useful for normal use. And replace it with a generic GPIO connector with as many pins as will fit.
If it can support 2 normal endstops (X and Y on a corexy) and a bed probe, that'll cover most use cases. Bed probes are usually either an inductive (5V+), or a bl-touch, or some kind of switch.

arrowcircle, 2021-10-21:
> Thanks for the hints. Looking at he BL-Touch docs it looks like all that is needed is a raw output PWM capable pin from the MCU, it will work with 3.3V for that PWM signal. I have considered moving the debug connector to pads on the back, they aren't really useful for normal use. And replace it with a generic GPIO connector with as many pins as will fit. If it can support 2 normal endstops (X and Y on a corexy) and a bed probe, that'll cover most use cases. Bed probes are usually either an inductive (5V+), or a bl-touch, or some kind of switch.

Hey @bondus! Thanks for the great work! Is bl touch already supported?

Seriyv0lk, 2021-12-08:
> Thanks for the hints. Looking at he BL-Touch docs it looks like all that is needed is a raw output PWM capable pin from the MCU, it will work with 3.3V for that PWM signal. I have considered moving the debug connector to pads on the back, they aren't really useful for normal use. And replace it with a generic GPIO connector with as many pins as will fit. If it can support 2 normal endstops (X and Y on a corexy) and a bed probe, that'll cover most use cases. Bed probes are usually either an inductive (5V+), or a bl-touch, or some kind of switch.

I think you can use 5 volts as the main supply voltage on the board and get 3.3 volts to power the microcontroller and the driver with an LDO, it doesn't need so much current that you need a step down regulator.This solves the problem with powering BlTouch, limit switches and other equipment that needs 5 volts, and the microcontroller you are using is most pins tolerant to 5 volts.

iPeel, 2022-02-17:
I'm using a BLTouch with the 0.61 board, to drive the control pin I had to use the CLK ( PA14 ) pin and take GND, 5V and an endstop input from the endstop connector.

[bltouch]
sensor_pin: ^head0:PB10 # Endstop 1
control_pin: head0:PA14 # CLK

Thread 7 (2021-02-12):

Toolboard Klipper version?

Unjun357, 2021-02-12:
Hello was not sure how to contact you other than on here. Does this board work with current master of klipper or does it require a branch version?

raymondh2, 2021-02-12:
It uses the master branch of Klipper from Kevin.

Closed 2021-04-15.

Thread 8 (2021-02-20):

Accelerometer?

Taudris, 2021-02-20:
Klipper semi-recently added support for using an accelerometer to help calibrate the input shaper. It would be awesome to have one built into this board (space and CAN bus bandwidth permitting).

bondus, 2021-04-15:
Version 2, which is being developed, will have an integrated accelerator. Have a look at HuvudTiny2.
We have tested wiring in an accelerometer to Huvud 0.50, it works fine.

brotherdust, 2021-04-15:
@bondus
> Have a look at HuvudTiny2.

Can you please provide a link to the HuvudTiny2? Interested in seeing how development is coming.

Closed 2021-04-15.

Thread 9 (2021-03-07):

Timeout on wait for 'tmcuart_response' response

boardthatpowder, 2021-03-07:
Using the Waveshare RS485 CAN HAT to control the Huvud board over CAN.

Tried both installation with Klipper master using [current](https://github.com/KevinOConnor/klipper/blob/master/docs/stm32f0_CAN.md) approach, as well as the [updated](https://github.com/KevinOConnor/klipper/blob/work-can-20210207/docs/CANBUS.md) approach on the klipper work-can-* branch.

Using the pins as described in your [sample printer.cfg](https://github.com/bondus/KlipperToolboard/blob/master/doc/printer.cfg) when attempting stepper moves (e.g. `M83, G1 E50`) the stepper successfully moves but shortly after Klipper crashes with the error `Transition to shutdown state: Timeout on wait for 'tmcuart_response' response`.

Any ideas?

boardthatpowder, 2021-03-07:
Looking at the klippy.log, looks like the tmc2209 is being shut down which is then causing the timeout:

```
TMC 'extruder' reports GSTAT:      00000001 reset=1(Reset)
```

boardthatpowder, 2021-03-09:
Figured this out. The [updated Klipper instructions](https://github.com/KevinOConnor/klipper/blob/work-can-20210207/docs/CANBUS.md) are missing this line which needs to be added to `/boot/config.txt`:

```dtoverlay=spi1-1cs```

Closed 2021-03-09.

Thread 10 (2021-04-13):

MCP2542FD on HuvudTiny2

madhunm, 2021-04-13:
Do you think replacing the SN65HVD230 with MCP2542FD  makes sense?

You have the CanHatFD; adding the MCP2542FD will extend the capability...

Also, what do you think about adding a rotary position encoder onto the back of the PCB? that way you could have a closed loop stepper driver.

bondus, 2021-04-13:
The STM32 used can not do CAN-FD, so an FD capable transceiver is not needed.
The old CAN2.0B is good enough, at 1mbps you can easily run 10 Huvud boards.

I did think about a rotation sensor, but imo it's not a good idea. It's easier to get a bigger stepper.

Closed 2021-04-13.

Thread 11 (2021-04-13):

Switching PSU on CanHatFD

madhunm, 2021-04-13:
If we could integrate a switching power supply to drop the V-In to 5v, we could avoid powering the Raspberry Pi over USB. I have not read much into the backpowering via the 5V pin; but, this is a feature you could consider.

Meanwell has a ready to use module: MDS15B-05 (18 ~ 36V in, 5V @ 3A out) Datasheet link: https://www.meanwell.com/webapp/product/search.aspx?prod=MDS15

They have a larger version as well: https://www.meanwell.com/webapp/product/search.aspx?prod=MDS20

I know they are on the larger side; but, they are usually fit and forget. No need to adjust the output voltage

bondus, 2021-04-15:
It actually has got 4 pins for an external DCDC converter, I have tested it with some cheap ali converter. There is a back-powering protection diode, a mosfet solution would avoid the voltage drop over the diode. It's currently not a good solution.

The board works but it's not being further developed at the moment. It's quite tricky to get the linux kernel driver working.

Those MDS parts are large but more importantly very expensive, not really viable for a product like this.

Thanks for the suggestions

Closed 2021-04-15.

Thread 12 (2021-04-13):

Endstop inputs

shavrin777, 2021-04-13:
Is it possible to add solder jumpers on the endstop inputs to disable pull-up resistors and RC filters so that these pins can be used as normal GPIOs? For example this can be used to connect servos or BLTouch.
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

bondus, 2021-05-01:
You can use the debug connector pins (SWDIN/SWDCLK and in some cases BOOT1) as GPIOs, they only have pull down resistors. There are two small pads on the back as well connected to PB10/PB11.
Servos and BLTouch requires 5V to run, so you would need a separate DCDC to supply them.

Closed 2021-05-01.

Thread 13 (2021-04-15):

Free up space on PCB

johnssarris, 2021-04-15:
You have so much crammed into this gem! If you need to free up space you might consider the following:

- Eliminate 2 of the mounting holes. Leaving 2 diagonal holes should be sufficient for mounting.

- Replace the MicroFit3 connector with one of the fancy NanoFit connectors.

brandonheller, 2021-04-15:
I'll give a contrasting opinion here - I had mounted a Huvud with the 4-pin pointing up, and realized recently that if I rotated it 90 degrees I can fit it much better into the available space.  Plus, I'm using all 4 holes to give rigidity to a mounting part.  With 2 holes, this wouldn't be possible.

bondus, 2021-05-01:
The NanoFit is a good alternative. It is a few mm narrower than the MicroFit.
Regarding the holes I think it's best to keep them all. But I can make the pads a bit smaller and move components a tiny bit closer, as long as you stick to hex bolts the heads of the screws are not very big. Every little 0.5mm makes a big difference.

Grogyan, 2021-05-04:
PCBs can have parts on the bottom side too, which enables even more space

Pakue95, 2021-05-04:
The disadvantage of placing parts on both sides would be higher manufacturing costs and worse mounting options due to interference with the components on the bottom.

Grogyan, 2021-05-04:
True it doesn't leave much in the way of mounting options.
But also false.

Slightly higher fabrication costs, but fairly negligible in volume manufacturing.

The alternative would be to have smaller parts.
Limitations on size are the connectors

I work in electronic manufacturing

bondus, 2021-10-06:
All good comment. It's designed for low volume <1k best case

Closed 2021-10-06.

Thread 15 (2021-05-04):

[FR]Thermocouple support

Grogyan, 2021-05-04:
Like many who are already using higher quality industrial sensors on their 3D printers.

This project was brought to my attention, as part of an ongoing effort to bring CAN Bus effectors to 3D printers.
With Marlin and Klipper firmwars in mind.

However, due to the need for reliability, thermocouple support is essential
Please consider a Thermocouple version

rlaferla, 2022-02-17:
Does the board support PT1000?

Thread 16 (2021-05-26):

Timeout on Wait for identify_response

antgeo, 2021-05-26:
Hi,

I'm having trouble establishing serial with the toolboard, the board is detected by ~/klipper/scripts/canbus_query.py but klipper fails to see a identify_response on start up. I've pasted my configurations below, it is interfacing with the Waveshare RS485 CAN HAT

> Created a socket
Wait for identify_response
Traceback (most recent call last):
  File "/home/pi/klipper/klippy/serialhdl.py", line 65, in _get_identify_data
    params = self.send_with_response(msg, 'identify_response')
  File "/home/pi/klipper/klippy/serialhdl.py", line 249, in send_with_response
    return src.get_response([cmd], self.default_cmd_queue)
  File "/home/pi/klipper/klippy/serialhdl.py", line 306, in get_response
    cmd_queue)
  File "/home/pi/klipper/klippy/serialhdl.py", line 241, in raw_send_wait_ack
    raise error("Serial connection closed")
error: Serial connection closed
Timeout on connect

My environment:

> ========= Last MCU build config =========
CONFIG_LOW_LEVEL_OPTIONS=y
\# CONFIG_MACH_AVR is not set
\# CONFIG_MACH_ATSAM is not set
\# CONFIG_MACH_ATSAMD is not set
\# CONFIG_MACH_LPC176X is not set
CONFIG_MACH_STM32=y
\# CONFIG_MACH_PRU is not set
\# CONFIG_MACH_LINUX is not set
\# CONFIG_MACH_SIMU is not set
CONFIG_STEP_DELAY=2
CONFIG_BOARD_DIRECTORY="stm32"
CONFIG_MCU="stm32f103xe"
CONFIG_CLOCK_FREQ=72000000
CONFIG_FLASH_START=0x8000800
CONFIG_FLASH_SIZE=0x10000
CONFIG_RAM_START=0x20000000
CONFIG_RAM_SIZE=0x5000
CONFIG_STACK_SIZE=512
CONFIG_STM32_SELECT=y
CONFIG_MACH_STM32F103=y
\# CONFIG_MACH_STM32F207 is not set
\# CONFIG_MACH_STM32F401 is not set
\# CONFIG_MACH_STM32F405 is not set
\# CONFIG_MACH_STM32F407 is not set
\# CONFIG_MACH_STM32F429 is not set
\# CONFIG_MACH_STM32F446 is not set
\# CONFIG_MACH_STM32F031 is not set
\# CONFIG_MACH_STM32F042 is not set
\# CONFIG_MACH_STM32F070 is not set
CONFIG_MACH_STM32F1=y
CONFIG_HAVE_STM32_USBFS=y
CONFIG_HAVE_STM32_CANBUS=y
\# CONFIG_STM32_FLASH_START_2000 is not set
\# CONFIG_STM32_FLASH_START_5000 is not set
\# CONFIG_STM32_FLASH_START_7000 is not set
\# CONFIG_STM32_FLASH_START_8800 is not set
\# CONFIG_STM32_FLASH_START_10000 is not set
CONFIG_STM32_FLASH_START_800=y
\# CONFIG_STM32_FLASH_START_0000 is not set
CONFIG_STM32_CLOCK_REF_8M=y
\# CONFIG_STM32_CLOCK_REF_12M is not set
\# CONFIG_STM32_CLOCK_REF_16M is not set
\# CONFIG_STM32_CLOCK_REF_25M is not set
\# CONFIG_STM32_CLOCK_REF_INTERNAL is not set
CONFIG_CLOCK_REF_FREQ=8000000
CONFIG_STM32F0_TRIM=16
CONFIG_CANSERIAL=y
\# CONFIG_STM32_USB_PA11_PA12 is not set
\# CONFIG_STM32_SERIAL_USART1 is not set
\# CONFIG_STM32_SERIAL_USART2 is not set
\# CONFIG_STM32_SERIAL_USART3 is not set
\# CONFIG_STM32_CANBUS_PA11_PA12 is not set
CONFIG_STM32_CANBUS_PB8_PB9=y
CONFIG_CANBUS_FREQUENCY=500000
CONFIG_USB_VENDOR_ID=0x1d50
CONFIG_USB_DEVICE_ID=0x614e
CONFIG_USB_SERIAL_NUMBER_CHIPID=y
CONFIG_USB_SERIAL_NUMBER="12345"
\# CONFIG_CUSTOM_STEP_DELAY is not set
CONFIG_INITIAL_PINS=""
CONFIG_HAVE_GPIO=y
CONFIG_HAVE_GPIO_ADC=y
CONFIG_HAVE_GPIO_SPI=y
CONFIG_HAVE_GPIO_I2C=y
CONFIG_HAVE_GPIO_HARD_PWM=y
CONFIG_HAVE_GPIO_BITBANGING=y
CONFIG_HAVE_STRICT_TIMING=y
CONFIG_HAVE_CHIPID=y
CONFIG_INLINE_STEPPER_HACK=y
=======================

/boot/config.txt

>dtparam=spi=on
dtoverlay=mcp2515-can0,oscillator=12000000,interrupt=25,spimaxfrequency=2000000
dtoverlay=spi1-1cs

/etc/network/interfaces.d/can0

>auto can0
iface can0 can static
        bitrate 500000
        up ifconfig $IFACE txqueuelen 128

Thanks!

lkong, 2021-06-04:
Had the same thing happen to me, try stop klipper wait a few seconds and restart klipper. If that doesnt work, do a firmware restart.

antgeo, 2021-06-04:
Resolved this. the RaspberryPi did not have a clean power source.

Closed 2021-06-04.

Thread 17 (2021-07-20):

Pins for the accelerometer?

blairq, 2021-07-20:
I could not see pins for the accelerometer.

Gnd, 3.3v , sclk miso and mosi?

bondus, 2021-07-20:
v0.5 was not designed specifically to have pins for it. But you can hook one up, there are some pads on the bottom (PB10, PB11) and you can use the pins on the debug connectors. I have not tested it myself, but I have seen others do it.

V0.6 will have an accelerometer on board, so there are no pins for it.

Closed 2021-07-28.

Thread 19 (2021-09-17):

ISOTP or ISOBus (J1939) for CAN protocol

olerem, 2021-09-17:
Hi, I was reading the Klipper CAN code and noticed that it is not using any protocols to send anything more then 8 bytes. This is not error proof especially for the "Waveshare Raspberry Pi CAN hat", the packets can be lost or go out of order.
I mainlined J1939 support to the Linux kernel, in case you are interested to implement it for Klipper - ping me, i'll try to help you.

bondus, 2021-10-06:
CAN adapters not adhering to the standard is out of scope for this projets

Closed 2021-10-06.

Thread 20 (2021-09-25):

Adapt design to RPI pico (rp2040 chip)

shaunmulligan, 2021-09-25:
Do you think it would be difficult or even feasible to adapt the design to make use of the rp2040 chip rather than the stm32? It seems the stm32s are impossible to buy at the moment and one can pick up single units of the pi pico for about €1. I think the one potential issue is that the pico doesn't have a native CAN implementation but it seems there are multiple implementations of it using the PIO pins.

Just wanted to get your thoughts on the possibility of the above, I am very interested in building a few of these boards but sourcing the parts is not super easy in the current environment :P

bondus, 2021-09-25:
The main issue with the rp2040 that I can see is the CAN bus, and the lack of 5V tolerant pins.
CAN bus should be doable with the help of the PIOs, but it's fairly complicated. I have not seen any full or even partial implementations of CAN bus on the rp2040 PIO. Interest is big so one will most likely appear, eventually.
Other than that it would be easy to CAD a new PCB and swap out the STM32.

shaunmulligan, 2021-09-28:
Yeah, I have had a look for a PIO based CAN implementation and it doesn't seem like it exists yet unfortunately but there do seem to be a number of people interested in it. Hopefully its just a matter of time 😄

Closed 2021-09-28.

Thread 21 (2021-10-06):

JLCPCB BOM/POS

necrogami, 2021-10-06:
MWSA0503-100MT according to LCSC is discontinued so not available anymore.
There are 2 SMD Resistors (R4,R7) that don't even show up as parts.

L4 and U3 show as no inventory available. Any possibilities of changing the pcb so that other parts can replace them?

bondus, 2021-10-06:
Things change a lot on component availability.

The resistors should be easy to find replacements for. R4 and  R7 are the current sense resistors for the stepper, quite critical components, you can use different resistances for them. 1% and 1/4W if I remember right.
Check the TMC datasheet for what's required and klipper documentation for how to configure.

U3, TPS54202/TPS54302/TPS54308 is out of stock everywhere I'm afraid.  L4 is a coil related to that.

I have been working on fitting a TPS54331 instead of the TPS54302, it does fit. But as a CS engineer it will take me 3 prototype rounds to get it right. It's tricky to get those voltage regulators to behave. Know any EEs?

necrogami, 2021-10-08:
I don't know any EE's i do know a CE, i studied electronics eons ago in hs but i figure i've lost more then remembered. I can ask around.

Closed 2023-08-07.

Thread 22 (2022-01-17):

Steathburner

Dragi2k, 2022-01-17:
Heyho,

is it possible to hook up a chamber thermistor on the board ?
and is it possible to control led via the board ? (5v excluding)

and wen it is possible how ?

Thank you

iPeel, 2022-02-22:
Yes, there's a second thermister input on PA1 if you wanted a roaming chamber temperature thermister, although IMO one on the gantry would suffice?

For controlling the Neopixel, there's GPIO pins you can steal from the diagnostics header, SWDCLK ( PA14 ) and SWDIO ( PA13 ) could both be used for this and the 5V output on the endstop header is rated for 2A, the Neopixels on the SB BOM would only use 210ma.

Unsure about the tacho signal, maybe one of the endstop pins would be OK for this?

Dragi2k, 2022-02-26:
thx for the anwere but i have the 0.50 not the 0.6 version ;-)

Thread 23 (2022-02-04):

Documentation updates for V0.61 version of board

eddietheengineer, 2022-02-04:
Hello! I love the Huvud boards--I have a ton of the V0.50 on my printers and just installed the first V0.61 on a printer last night! There were a few gotchas/clarifications as more people install this:

Add flashing instructions
-8Mhz clock for make menuconfig build
-Add note -- if the wrong bootloader option is selected and you try to flash the Huvud, it will not work--need to flash the bootloader again using an ST-Link

Updated pin descriptions:
Thermistor 1 - PA0
Thermistor 2 - PA1
Heater - PA6
Fan 1 - PA7
Fan 0 - PA8
Endstop 1 - PB10
Endstop 2 - PB11
Endstop 3 - PB12
ADXL CS pin - PB1
Diag for TMC2209? - PA15

rlaferla, 2022-03-03:
There are three pins on the thermistor, what is the mapping?
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

rlaferla, 2022-03-07:
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

rlaferla, 2022-03-18:
I can't seem to flash it.

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

rlaferla, 2022-03-18:
Newer Waveshare boards have a 12M clock and not a 8M!

rlaferla, 2022-03-19:
I was able to get it to work.  The crystal speed in menuconfig must be 8M because it's the Huvud crystal and NOT the Waveshare one (which was 12M in my case.)

rlaferla, 2022-04-05:
SWDIO PA13?

charlespick, 2022-05-22:
+1 would like the docs to be updated with more detailed information about how to use the new adxl, single canbus/power connector, multiple endstops and thermistors, and terminating the canbus using the pads on the back.

dpoulson, 2022-11-05:
> I was able to get it to work. The crystal speed in menuconfig must be 8M because it's the Huvud crystal and NOT the Waveshare one (which was 12M in my case.)

Could you say how you managed to get it to work? I'm having the same issues, using the same settings as you. Output from make flash is exactly the same as above. (with different size of firmware of course)

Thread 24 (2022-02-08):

Question: running this on a 12v system

varazir, 2022-02-08:
Hello,

I like this idea and been looking for a solution for my Wanhao i3 v2.1.
Found this when I watched eddietheengineers video. He mentioned that he had issue with 12v system.
Could you add some type of heat sink to the board to alleviate the heat?

I have moded my printer with a BLTouth probe and dual 12v blowers for part cooling.

TIA
Daniel

bondus, 2022-02-15:
It will work perfectly fine with a standard 40-50W hot end heater at 12V
I do not recommend running it with a heater over 5A (60W at 12V)

Closed 2022-02-15.

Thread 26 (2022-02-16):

Inductive probe?

rlaferla, 2022-02-16:
Does this board support an inductive probe (Omron)?

rlaferla, 2022-02-21:
I was hoping to get some info here.  I see there is an endstop connector.  Can I use it for a Klicky probe?

iPeel, 2022-03-17:
You should be able to use an "n type" inductive probe, but Klicky or Euclid is an easier fit. On the 0.61 board there are three endstops and any one of them will work for the probe. I've use BLTouch and Klicky but haven't tested an inductive probe.

cjkzwe, 2022-07-23:
@iPeel Do you know how to write config if I want to use Klicky as a probe and connect two endstops at the same time on the 0.61 ver board?

iPeel, 2022-07-25:
@cjkzwe that shouldn't be a problem, there's three endstop inputs so you can use endstop 1 (PB10) for Klicky, endstop 2 (PB11) for X and endstop 3 (PB12) for Y.

example snippets:

#Huvud MCU definition
[mcu head0]
serial: /dev/serial/by-id/usb-Klipper_stm32f103xe_52FF6D064850775026211367-if00
restart_method: command

[probe]
pin: ^head0:PB10

[stepper_x]
endstop_pin: head0:PB11

[stepper_y]
endstop_pin: head0:PB12

Not sure if you'll need ^'s on the endstop pins as I haven't converted mine yet.

cjkzwe, 2022-07-26:
@iPeel Thanks a million! I'll try this config as my board is ready.

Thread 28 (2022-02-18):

USB details

ModMike, 2022-02-18:
Can you provide some documentation of the USB functionality? I only need 1 tool head board so I don't need to daisy chain it.

1) How do I enable it?
2) Do I need to use USB power lines in addition to the main power?

Thanks for an AMAZING board. Best idea ever.

iPeel, 2022-02-20:
If you look at the back of the 0.61 PCB there's 6 pads in two columns between the Microfit3 connector and the USB connector but on the other side of the PCB. The top 2 pads are the USB D+ and D- and the bottom pads are the Canbus + and -, the middle are the Microfit3 data pins. There are tracks between the canbus and microfit pads, cut these with a knife then solder bridge between the USB and the Microfit pads, this effectively turns the microfit3 connector into running USB instead of Canbus.

You can then wire the microfit3 cable up to a USB type A, but don't take the ground from the USB or the power from the USB, just the D+ and D-. I used some sheilded cable to run from the USB, complete with the sheild but didn't terminate the sheild at the Huvud end. USB D+ is on the same side as the 24v+ and USB D- is on the same side as the power -.

Then, follow the instructions for flashing the Huvud board ( STM32, 2K bootloader etc ) but instead of using Canbus, choose to use USB. You can even flash the Huvud board over the USB going to the Microfit3 connector and this will confirm the USB is working.

To configure Klipper it's the same as any other USB board, look for its identity in /dev/serial/by-id and set this as the Serial in the MCU configuration:

[mcu head0]
serial: /dev/serial/by-id/usb-Klipper_stm32f103xe_53FF6D064848885546352367-if00
restart_method = command

ModMike, 2022-02-20:
Thank you SO MUCH! I am fine with the CAN hat (have 3 on the way) I just wanted to avoid using GPIO in case I need them in the future. I understand that I am only using 2 and I can add a ton of devices on CAN. It also seems like USB will be easier to maintain via flash.

clawszilla, 2023-05-04:
Should I still have continuity between the d+ and d- and the Vin and GND on the microfit connector pins? Or is that going to cause a problem when I wire it to 24v? I'm worried I cut the pads too deep or something.

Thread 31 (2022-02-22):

Can use RP2040?

spectrespc, 2022-02-22:
Can use RP2040? STMs have become very expensive :(
https://jlcpcb.com/parts/componentSearch?isSearch=true&searchTxt=rp2040

bondus, 2022-02-28:
The major stopper is that the RP2040 does not have CAN bus.
It should be possible to implement using the PIOs, I was hoping the community would have done that already.
Or possibly use an external CAN controller over SPI bus

wattsie, 2022-04-25:
Ill just leave these here for reference.
The MCP2518FD is like $2aud on digikey
https://kentindell.github.io/2021/02/16/three-pico-boards/
https://www.cnx-software.com/2021/12/15/canbed-raspberry-pi-rp2040-board-supports-can-bus-obd-ii-protocol/
Cheers.

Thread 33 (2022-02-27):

Questions: Alternate TMC driver setup

flackenstein, 2022-02-27:
What are you thoughts on using a TMC driver module with a low profile header?  This way if the driver goes bad it can be quickly and easily replaced.  This also allows us to upgrade the driver module to alternate versions.

Example Module: https://www.digikey.com/en/products/detail/trinamic-motion-control-gmbh/TMC2209SILENTSTEPSTICK/10232488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

Example Low Profile Header: https://www.digikey.com/en/products/detail/samtec-inc/TLW-108-06-G-S/1105092

Other benefit, if you use taller headers for the TMC driver you can place component underneath to maximize footprint.

flackenstein, 2022-02-28:
Worth adding it's a lot easier to procure the Trinamic SilentStepStick in the Americas and it has a unit cost that isn't that much more than the IC itself, and makes for easier repairs/upgrade.

https://www.trinamic.com/support/eval-kits/details/silentstepstick/

bondus, 2022-02-28:
There are a few downsides to having a stepstick/modular solution:
1. Thermals is a lot worse. When mounting the driver directly to the board the whole board acts as a heatsink
2. Cost and complexity of a modular approach is higher.
3. Connectors use up a lot of precious board space. As you say some can be mitigated by the ability to put components under the module.

For now I think the better solution is to have the driver directly mounted to the main board.

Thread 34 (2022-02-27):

Question: Endstop Header VCC

flackenstein, 2022-02-27:
Would it be possible to jumper the VCC on the .6x revision to support either 3.3V or 5V?  Depending on the hardware used this would allow for broader support.

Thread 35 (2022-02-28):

Thermister accuracy at low temperatures ( E3D V6 )

iPeel, 2022-02-28:
I have an issue with the thermister reading at low temperatures ( below 10 degrees celcius ). When I start up Klipper shuts down through an ADC threshold error, I have to blast the hot end with a heat gun to get the firmware to start. It seems the thermister on my 0.61 board is out by about 10 degrees at lower temperatures compared to the bed temps but fine at higher temperatures.

The pertinent bits from my extruder section are:

heater_pin: head0:PA6
sensor_type: ATC Semitec 104GT-2
sensor_pin: head0:PA0
pullup_resistor: 2200
min_temp: 0
max_temp: 300

Anyone else find this, or am I configuring something wrong?

iPeel, 2022-03-17:
In the end I resolved this by lowring the pullup_resistor value by a couple of hundred ohms in the Klipper config. Seems to report fine at both low and high temps.

jakep82, 2022-03-23:
I'm having a similar issue, and I've done some testing to confirm something isn't right.  I connected a PT1000 and a ATC Semitec 104GT-2  to TH1 and TH2 on the Huvud, and installed them in the same heater block for testing (both configured with 2200 ohm pullup).  In a 20C room, the PT1000 shows around 20-21C, but the thermistor is reading around 13-14C.  Using the PT1000 to control the hotend and heating it up so the PT1000 reads 230, the thermistor reads around 250.  I've checked resistance values on both the thermistor and the PT1000 at a couple known temperatures (0C and 20C), and both seem within tolerance of expected values.

The PT1000 is definitely reading too low at operating temp, because printing ABS at my normal 235C temp resulted in print issues I associate with overheating the filament.  By contrast the thermistor is reading way too low at room temp, but seems like it might be accurate at normal print temps.

I'll be receiving a thermocouple today to do more testing.

iPeel, 2022-04-12:
@jakep82 that's interesting, let me know what your testing comes up with. Did you try amending the pullup_resistor value in ther config and if so what effect did that have on the top end readings?

jakep82, 2022-04-12:
I tested a Dragonfly and a V6 with my thermocouple inserted down into the nozzle of each hotend.  Both thermistors I tested read 5C low at 235C (Klipper reporting 235C on thermistor, thermocouple reading ~240C).  Most of this can likely be attributed to the fact that nozzle is in between the heater and the thermistor.

My PT1000 by contrast was reading 10C low at print temps (235C on PT1000, ~245C on thermocouple).  This is why my prints seemed too hot with the PT1000.

In the end I'm using the stock 2200 resistor value with regular thermistors.  Somewhere around 50-60C the values on the thermistors correspond directly with the thermocouple.  This is in the typical range for my chamber temps, so it all works out for me.  I just ignore the room temperature readings.

iPeel, 2022-05-03:
@jakep82 thanks, this inspired me to buy a decent thermocouple and measure mine too from the inside of the nozzle. You are correct in that with the stock 2200 pullup config the values are out at the lower end but at operating temperatures seem accurate with within a few degrees. With an amended pullup resistor config the values were accurate at the low end on startup but were off by 10-15 degrees at operating temperatures.

I've reverted to the default config now, but it means in the winter when I start up in a cold workshop I'll have to hit the hotend with a hot air gun before switching the printer on to avoid startup errors.

jakep82, 2022-05-03:
@iPeel Just change the min_temp on all your sensors.  No need to use a heat gun.

I should also mention I ended defining a custom thermistor to improve accuracy.  I used the QUERY_ADC function in Klipper to pull the raw values with a 2200 pullup at known temperatures I was measuring with my thermocouple.  By defining values at room temp, 50C, and 240C my thermistors are now accurate to within a few degrees throughout the range where I use them, including room temp.

iPeel, 2022-05-05:
@jakep82 I've never succeeded in configuring a min_temp below 0 degrees, I don't think it's allowed. In the winter my workshop drops to only a few degrees and this results in a negative reading on the Huvud. At the moment it's not an issue but later in the year I'll probably resort to a custom map if nothing else emerges in the meantime.

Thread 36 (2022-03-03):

Waveshare RS485 + Pi Zero W 2

rlaferla, 2022-03-03:
Is this still an issue with the new Pi Zero W 2?  The new Pi is 5x faster than the original.  I am looking to use it with 1 toolhead w/ADXL.  In the future, I'd like to upgrade to 2 toolheads w/ADXL.

> The MCP2515 is a very common SPI connected CAN bus chip. It is a pretty bad options since it has very small buffers on chip and creates a lot of CPU load on the Raspberry Pi, and has a tendency to drop packet. It is not recommended if you use more than 1 or 2 boards or if you plan to use the accelerometer.
>
> You have to run the CAN bus at 250kbits/s or possibly 500kbits/s. An older Pi, or a Pi Zero will not work reliably, it has to be a Pi3 or Pi4 or better.

rlaferla, 2022-04-05:
You can't use a Pi 0 W2.  I had all sorts of issues until I upgraded to a Pi 4.

Closed 2022-04-05.

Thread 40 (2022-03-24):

Klippy shutdown:  Timeout on wait for 'tmcuart_response'

rlaferla, 2022-03-24:
I have Huvud 0.61 mostly working with Raspberry Pi Zero W 2 and Waveshare RS485/CAN HAT but it's shutting down all of a sudden with this error.

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

rlaferla, 2022-03-24:
Is it CAN bus cable issue?  I am using a Molex overmolded cable that does not have twisted pairs nor is shielded.

rlaferla, 2022-03-24:
Is it a heatsink issue for the TMC driver?  I do not have a heat sink on it and I don't know where to find one that would fit or how to place it on the Huvud.

rlaferla, 2022-03-24:
Is it a baud rate issue?

rlaferla, 2022-03-24:
Timeout with MCU 'can_mcu' (eventtime=255.368785)
Stats 255.4: gcodein=0 mcu: mcu_awake=0.001 mcu_task_avg=0.000005 mcu_task_stddev=0.000004 bytes_write=16565 bytes_read=26641 bytes_retransmit=9 bytes_invalid=0 send_seq=1053 receive_seq=1053 retransmit_seq=2 srtt=0.001 rttvar=0.000 rto=0.025 ready_bytes=0 stalled_bytes=14 freq=180004231 can_mcu: mcu_awake=0.001 mcu_task_avg=0.000008 mcu_task_stddev=0.000007 bytes_write=3092 bytes_read=13883 bytes_retransmit=82 bytes_invalid=134 send_seq=317 receive_seq=312 retransmit_seq=316 srtt=0.001 rttvar=0.000 rto=3.200 ready_bytes=0 stalled_bytes=0 freq=72001016 adj=71999344  heater_bed: target=0 temp=21.0 pwm=0.000 sysload=0.13 cputime=20.095 memavail=189492 print_time=85.489 buffer_time=0.000 print_stall=0 extruder: target=0 temp=22.6 pwm=0.000
Got error -1 in can write: (105)No buffer space available
Got error -1 in can write: (105)No buffer space available
Got error -1 in can write: (105)No buffer space available
Got error -1 in can write: (105)No buffer space available
Got error -1 in can write: (105)No buffer space available

rlaferla, 2022-04-05:
I upgraded from a Pi Zero W 2 to a Pi 4 and the problem went away.  Even though the Pi 0W2 is 5x faster than the Pi 0W, it's not enough.

Closed 2022-04-05.

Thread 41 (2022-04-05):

How do you connect the StealthBurner LEDs to Huvud 0.61?

rlaferla, 2022-04-05:
How do you connect the StealthBurner LEDs to Huvud 0.61?

Trippinonaduck, 2022-06-01:
5V from the endstop connector, and then ground and PA14 from the pins above.

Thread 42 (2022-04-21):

STEP file of board assembly

blalor, 2022-04-21:
Would it be possible to get a STEP file of the assembled board?  This would really help with figuring out clearances on dense toolheads.

blalor, 2022-04-23:
WiggyWooSaa#2095 [shared](https://discord.com/channels/582187371529764864/806270404279926804/967078653370466385) a STEP file on the Rat Rig Discord. Attached.

[Huvud_v.61_v2.step.zip](https://github.com/bondus/KlipperToolboard/files/8546680/Huvud_v.61_v2.step.zip)

blalor, 2022-04-24:
Oops, I hadn't seen #38. 😐

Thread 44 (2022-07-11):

3 axis version

gielbloks, 2022-07-11:
is it possible to add 3 steppers onto the board?
by tapping into 4more pins from th stm32f103?

this is needed for a pan/tilt function on my printer as well as the extruder,or can you bring out a version with 2 extra stepper motor driver inputs? (connection solderd directly on the stepstick)

don't need 3 boards on the gantry this way (weightsavings)

regards giel

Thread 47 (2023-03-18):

Future design iteration suggestion - Angled Pin Header

TheFuzzyGiggler, 2023-03-18:
Just a suggestion for a future iteration.

The pin headers for the ST-LINK programming are taller than the surrounding connections.
I have a Voron 2.4 and I use the Huvud board on the X/Y (A/B) motors.
If the gantry is crooked (which can happen if the printer is off and you lean on the back gantry rail like an idiot)...
and you go to home, you can crash the back rail into the bottom plate.

Since the pins of the header are the highest point, they impact first and they bend.

Picture below was AFTER I had straightened most of them, they were essentially bent down on top of each other.
I'm shocked I didn't fry the board by shorting power and ground.

Next iteration maybe use a 90 degree header so these pins aren't the first thing to hit if a stepper goes too low?

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

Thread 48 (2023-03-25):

Timeout on wait for 'tmcuart_response' response

Varunclotux, 2023-03-25:
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
I am having problems with Klipper since this is my first time using it. I am getting errors one after another now.

Closed 2023-03-29.

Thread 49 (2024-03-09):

Steps required to restore a damaged bootloader

ssvenn, 2024-03-09:
I bought a used Huvud board that I accidentally bricked with a bad flash update, it had an old version of CanBoot on it from the previous owner and I compiled Klipper with the wrong bootloader offset (2k instead of 8k), and the CanBoot bootloader happily overwrote part of itself while flashing.

I didn't find any clear documentation on how to restore the bootloader on the Huvud but have been looking at the datasheet for the STM32F103 and it seems this chip does not support bootloader recovery through USB, only UART. And those UART pins are in use by the stepper driver I believe, while the pins that go to the jumper header block are used for the stock bootloader?

Am I right in thinking that the chip would have to be desoldered to be reflashed?

bondus, 2024-03-09:
You can use a ST-Link programmer to flash a new bootloader. The 6-pin header has the necessary pins. You can find cheap clones "ST-Link v2" on most
You might have to connect the test points boot0 "B0" and 3.3V on the backside to force the CPU into the ROM bootloader.

ssvenn, 2024-04-02:
Thanks, can confirm that a clone ST-Link programmer was able to erase and reflash the board!

Closed 2024-04-02.

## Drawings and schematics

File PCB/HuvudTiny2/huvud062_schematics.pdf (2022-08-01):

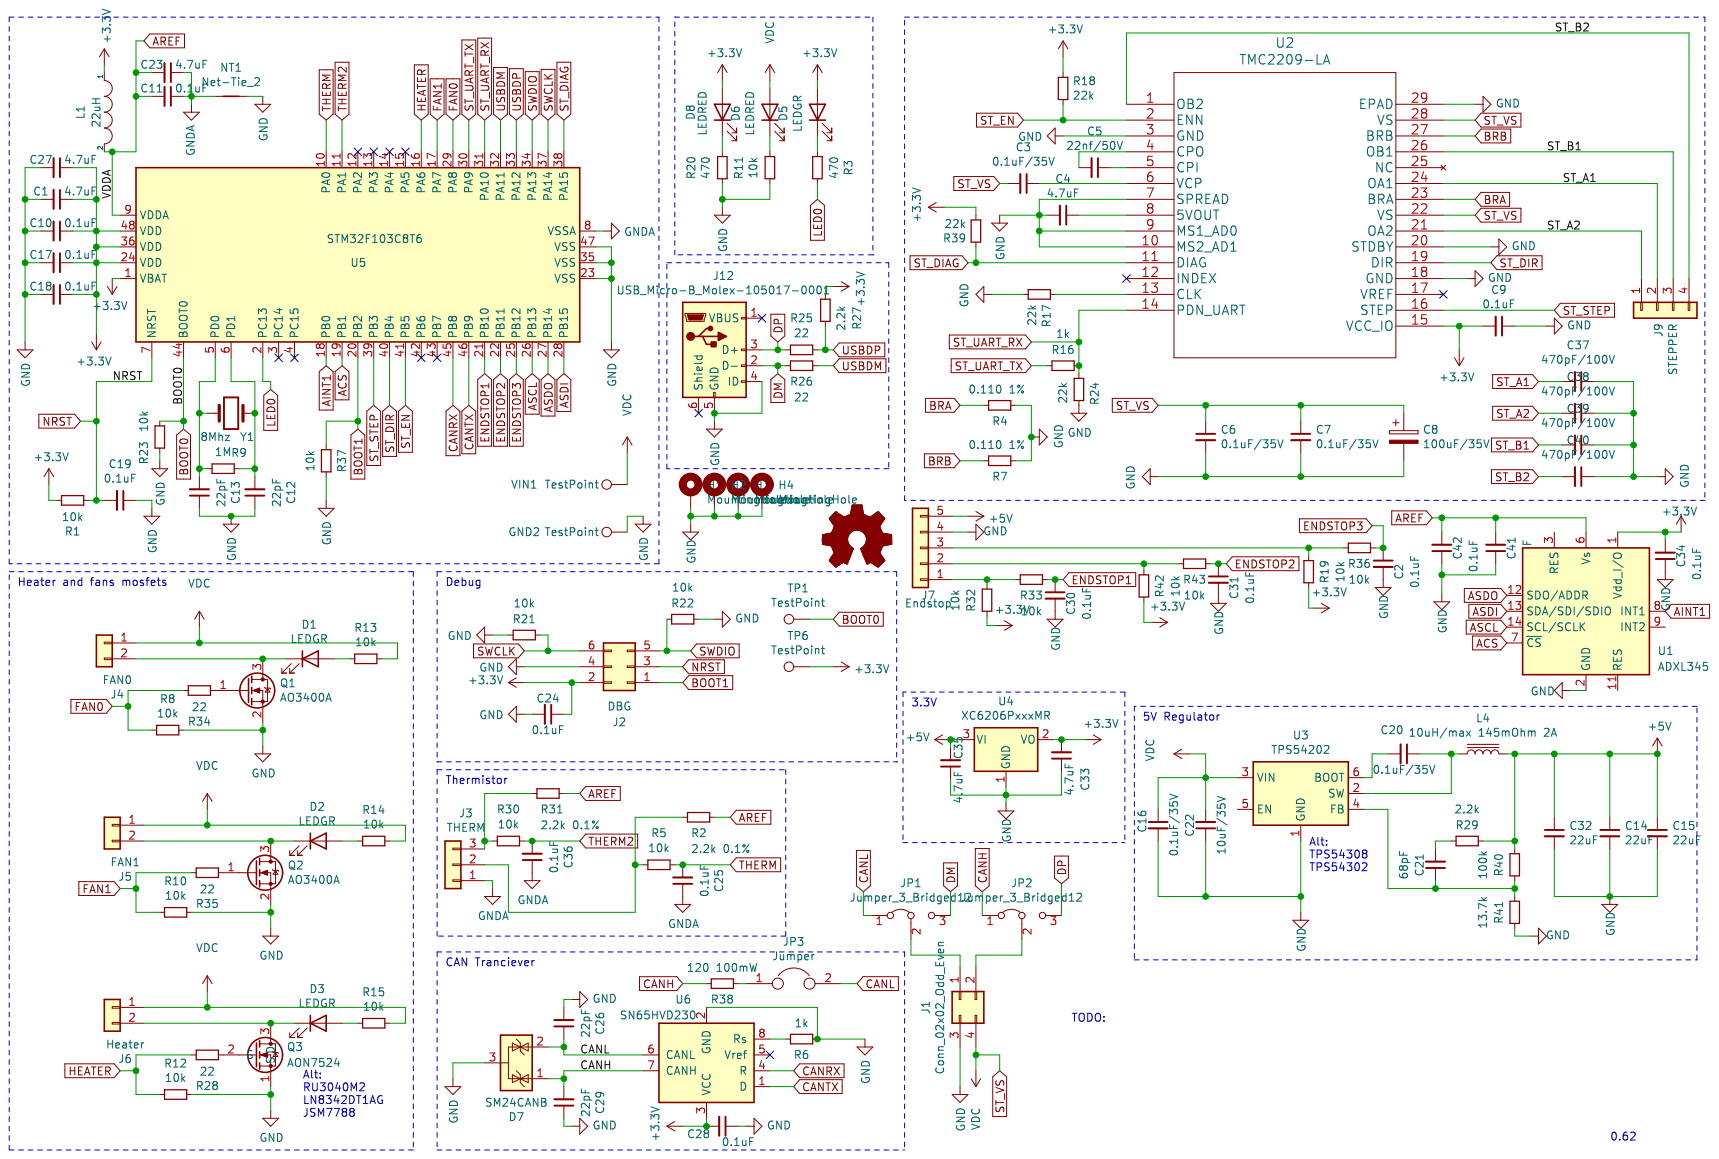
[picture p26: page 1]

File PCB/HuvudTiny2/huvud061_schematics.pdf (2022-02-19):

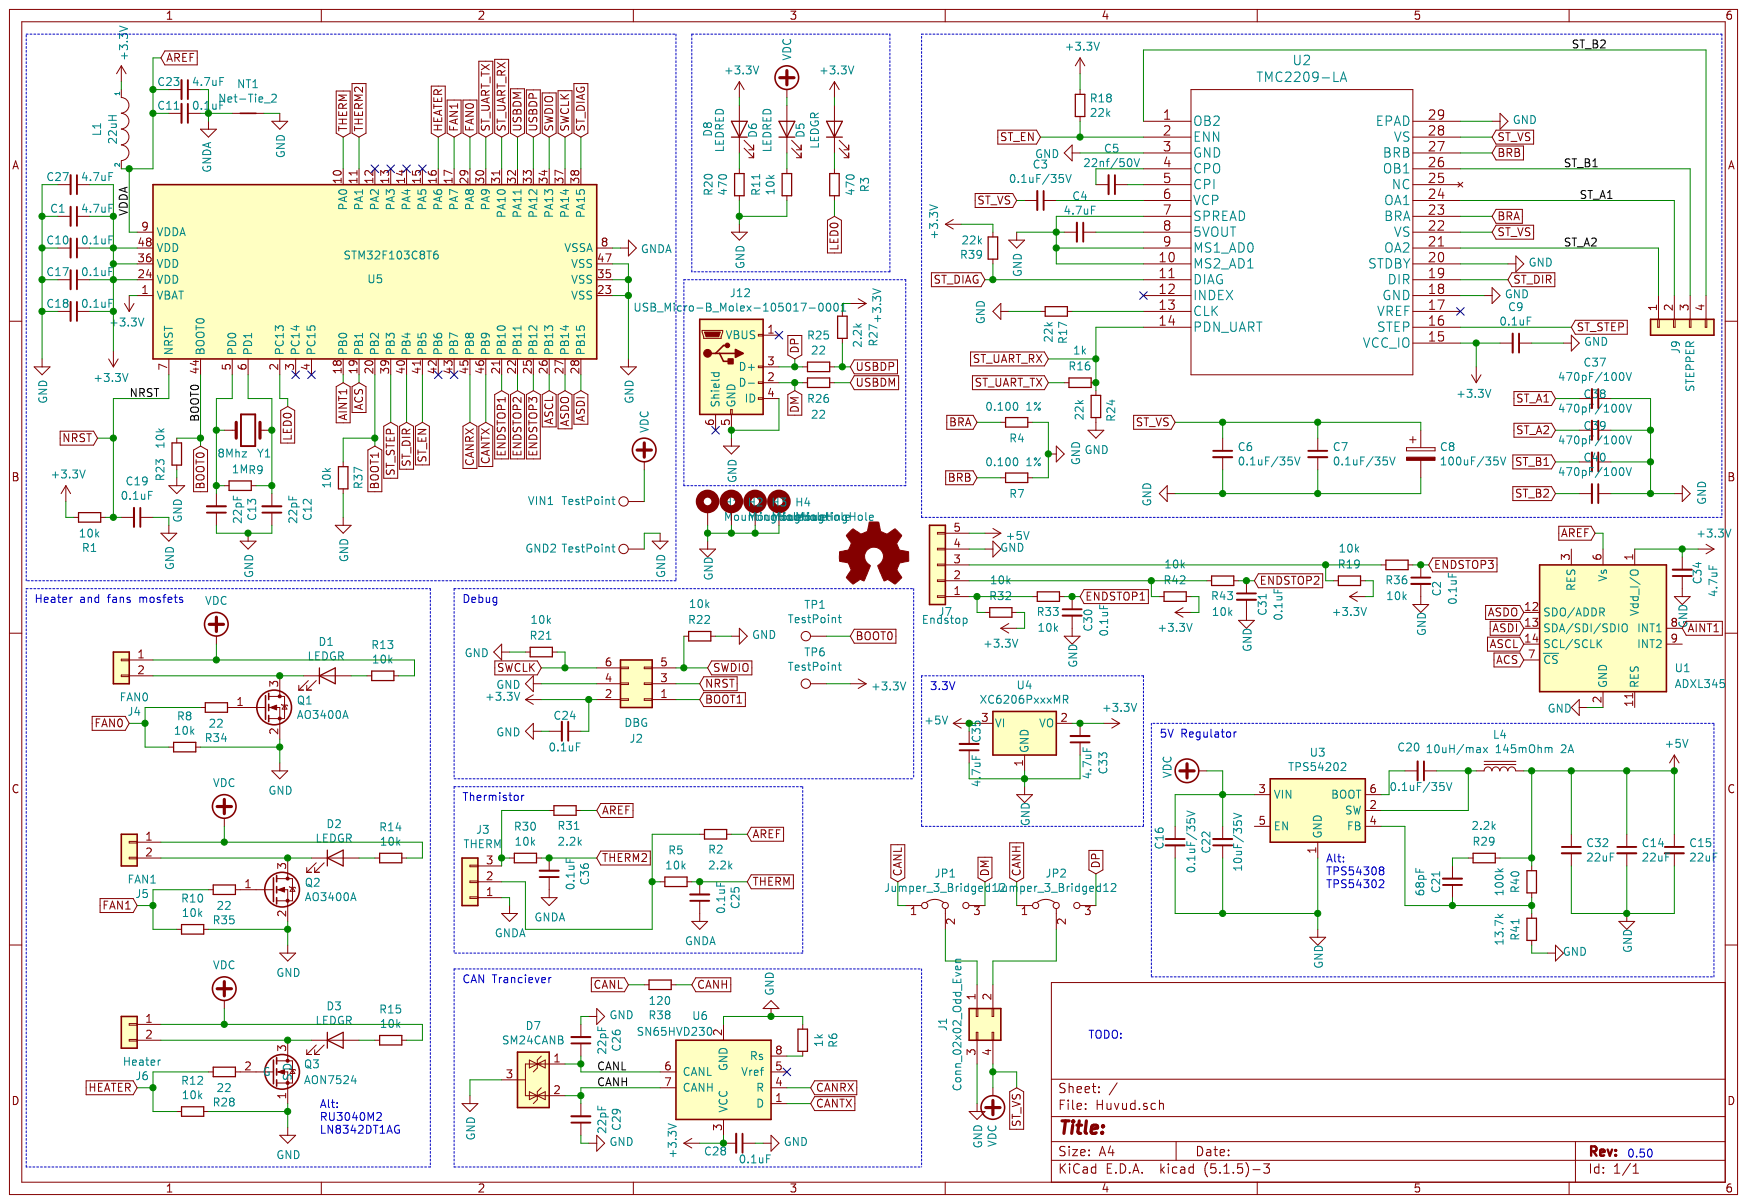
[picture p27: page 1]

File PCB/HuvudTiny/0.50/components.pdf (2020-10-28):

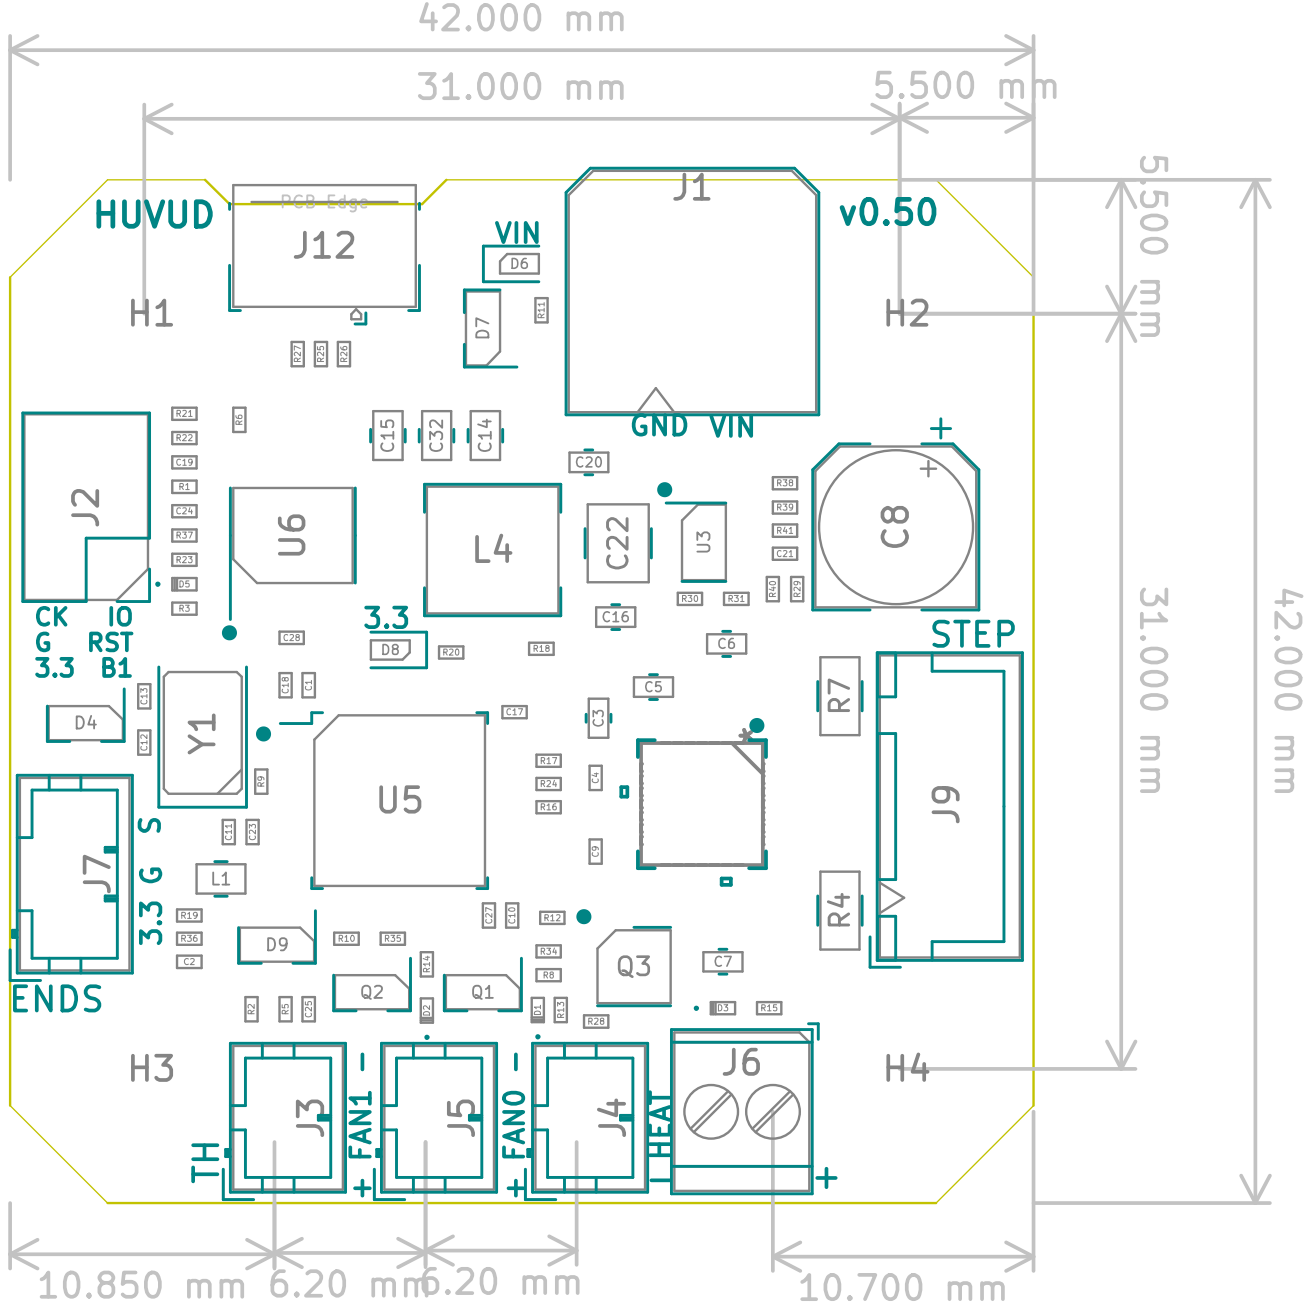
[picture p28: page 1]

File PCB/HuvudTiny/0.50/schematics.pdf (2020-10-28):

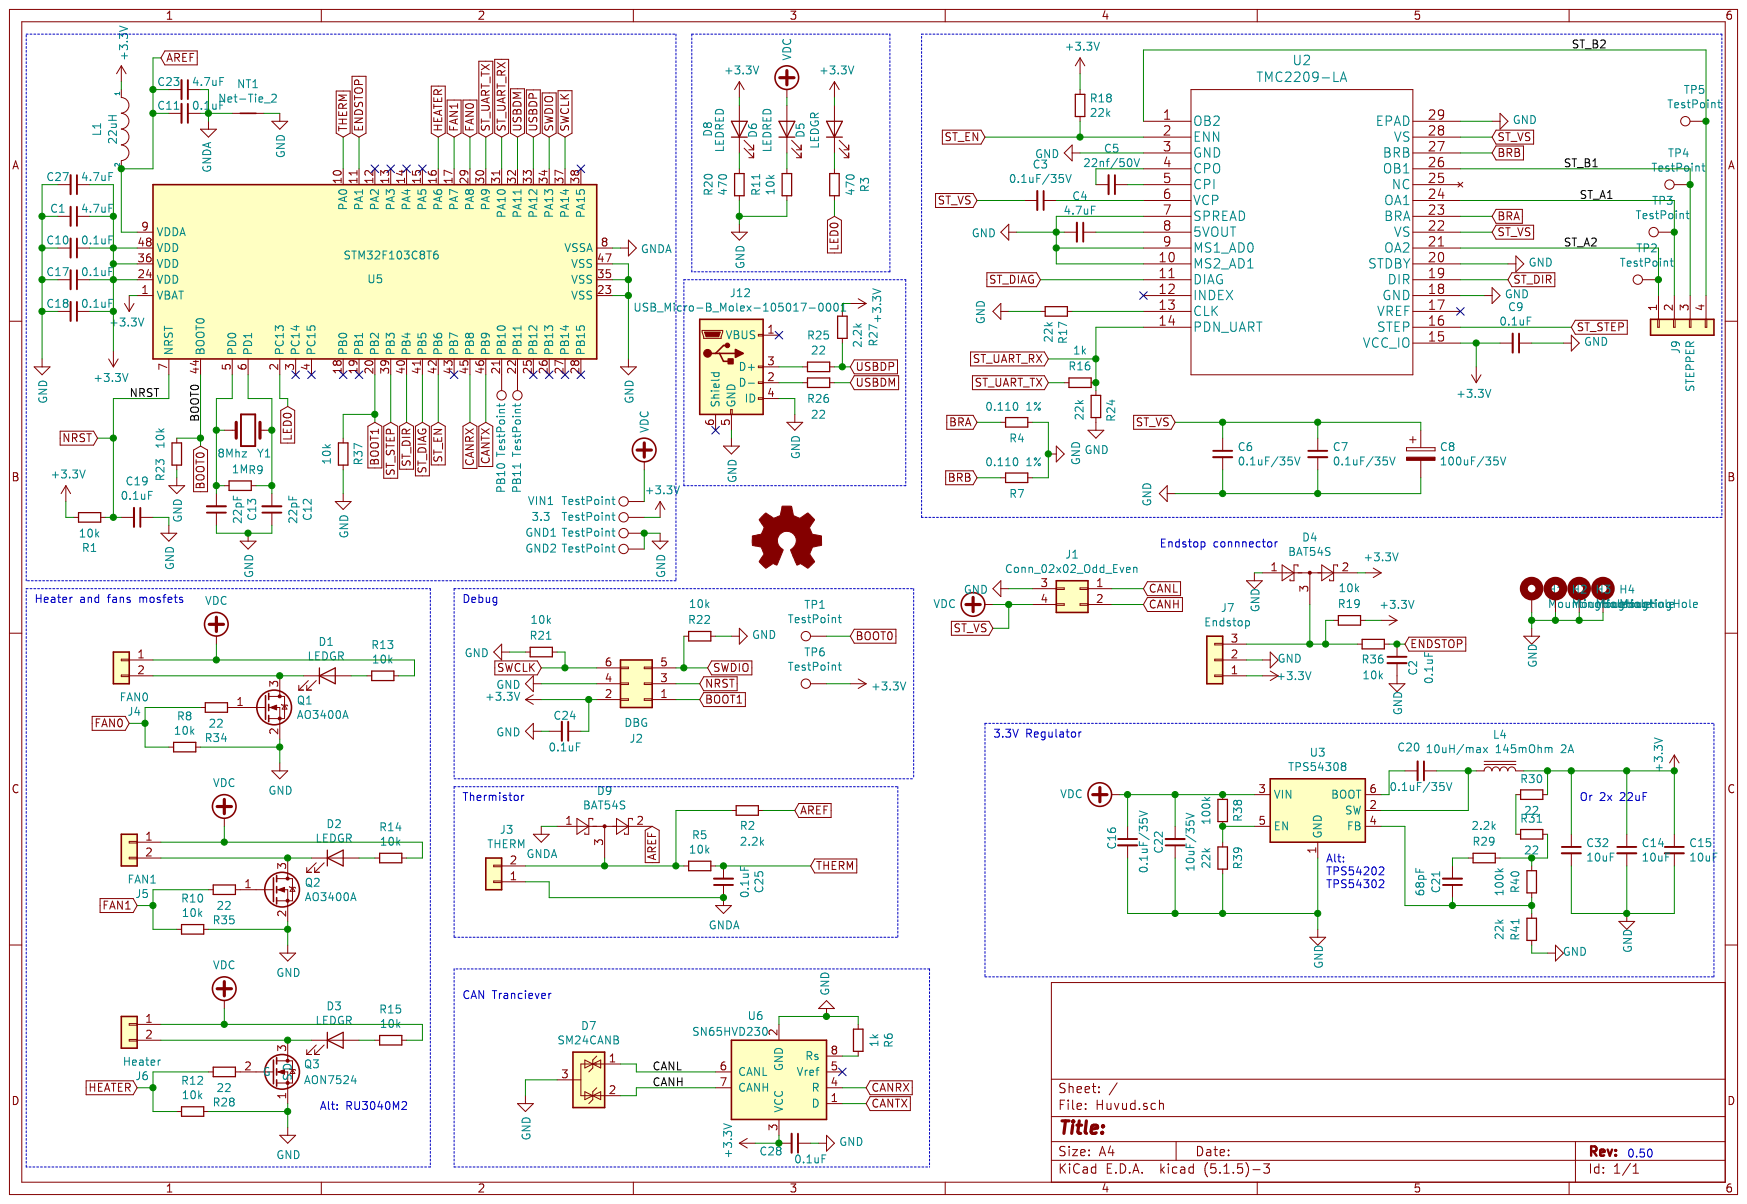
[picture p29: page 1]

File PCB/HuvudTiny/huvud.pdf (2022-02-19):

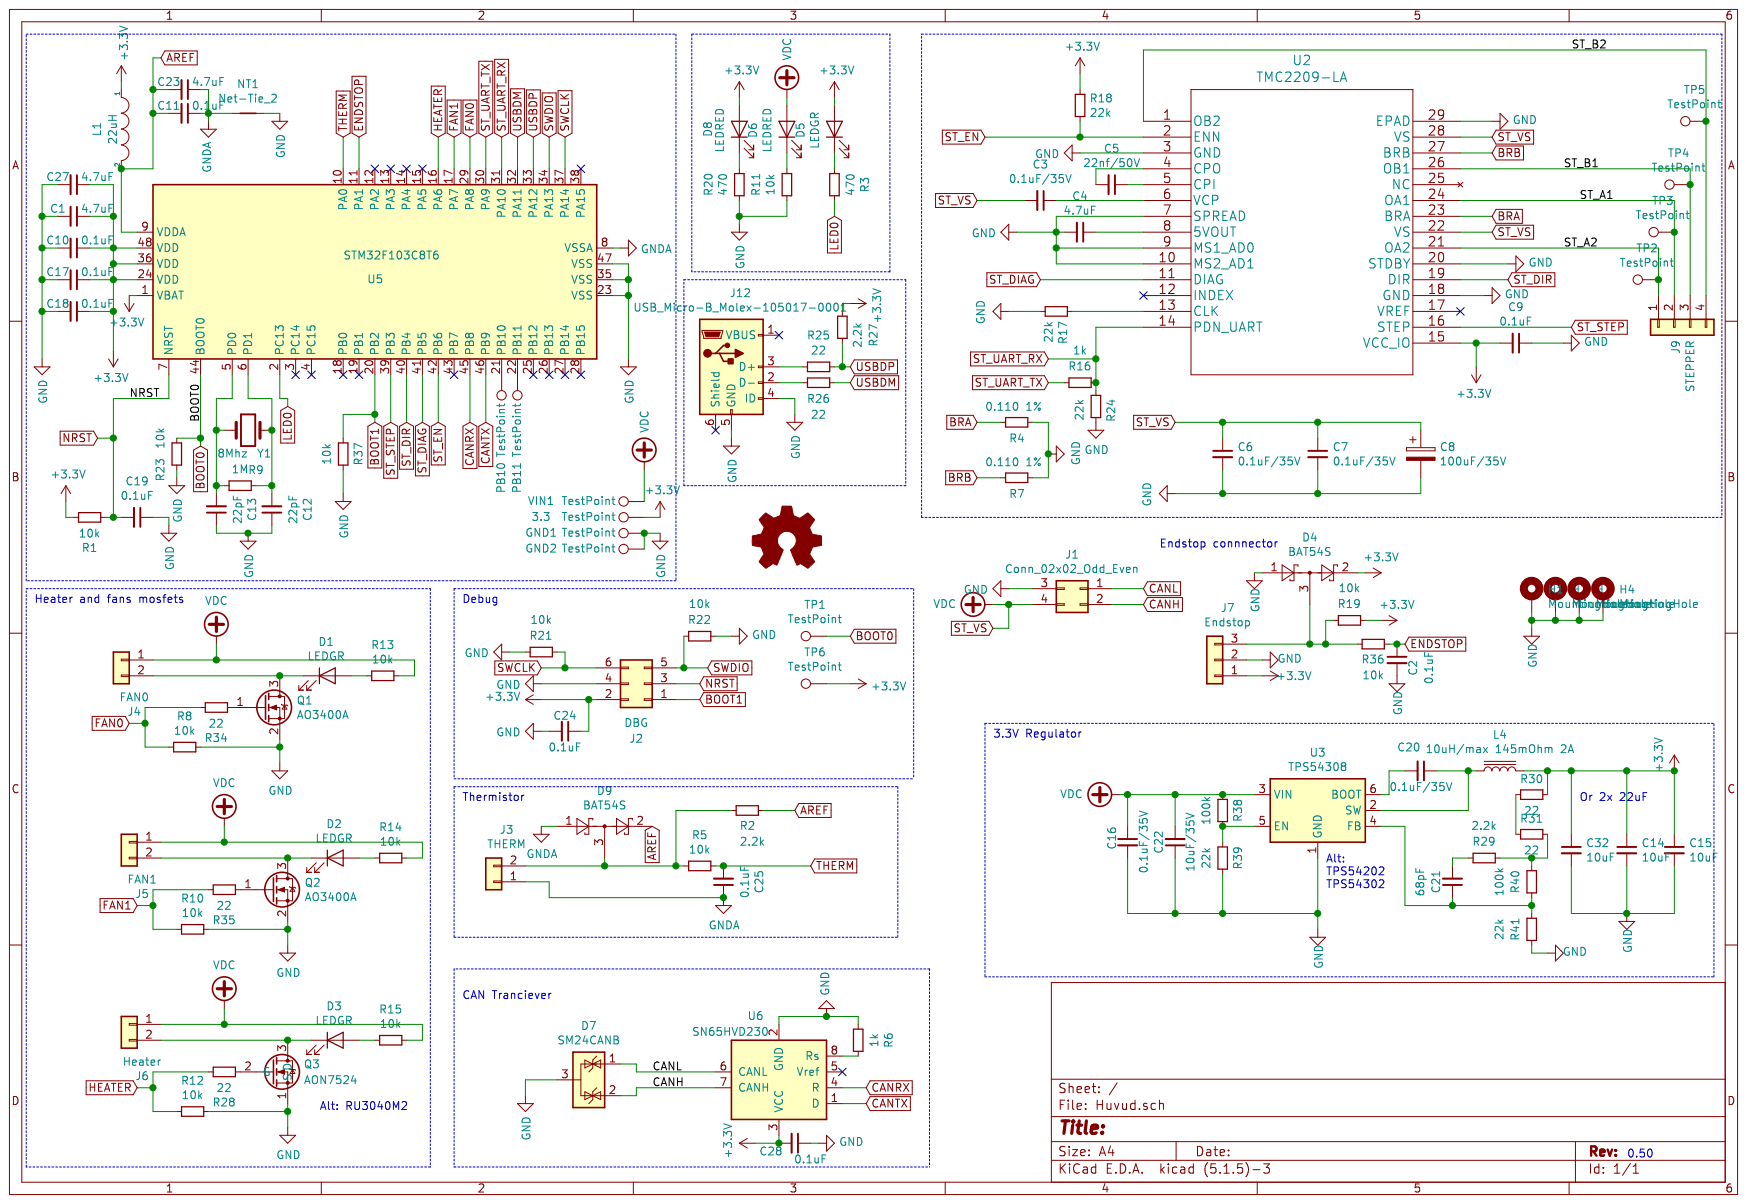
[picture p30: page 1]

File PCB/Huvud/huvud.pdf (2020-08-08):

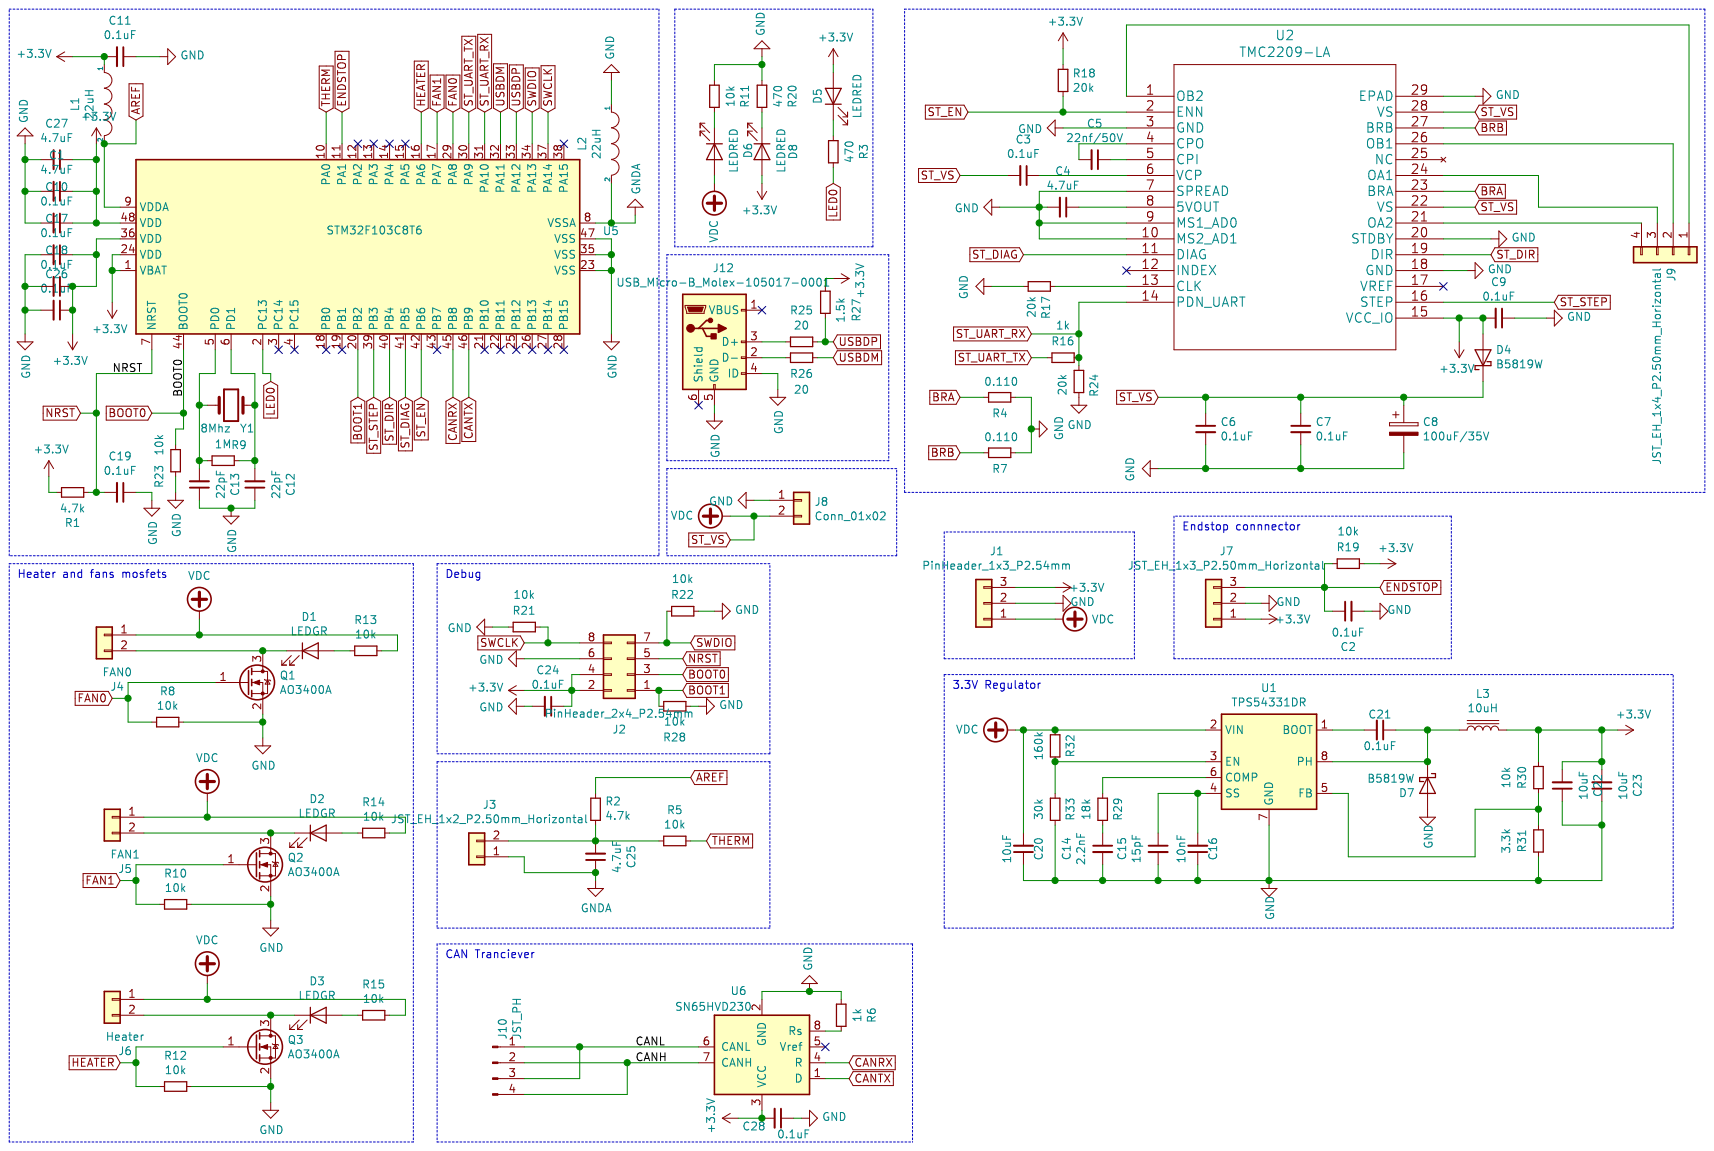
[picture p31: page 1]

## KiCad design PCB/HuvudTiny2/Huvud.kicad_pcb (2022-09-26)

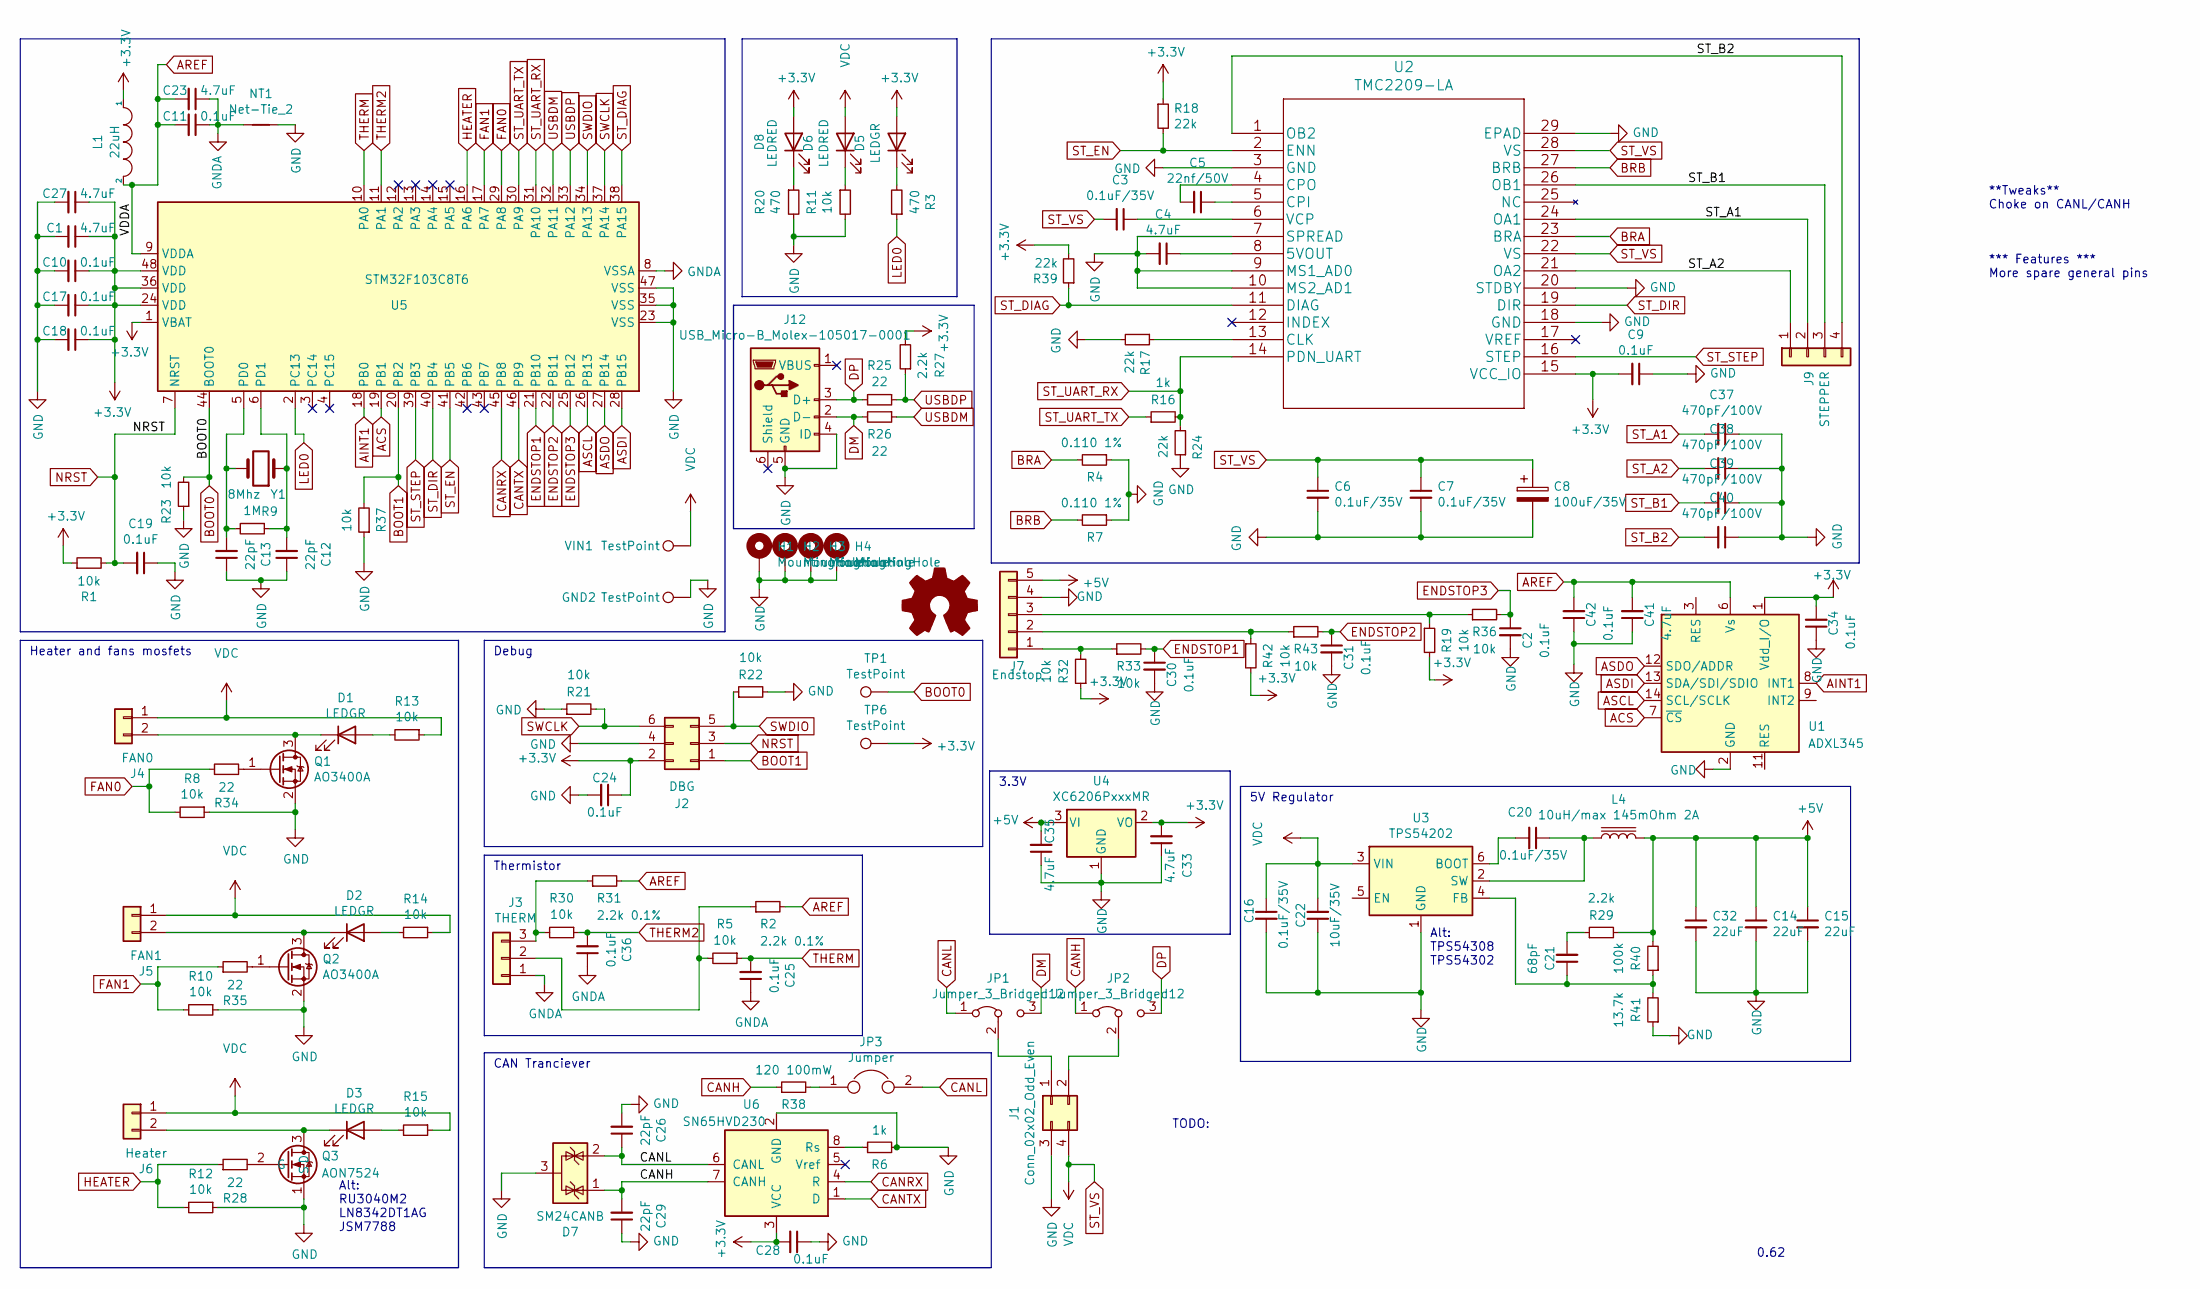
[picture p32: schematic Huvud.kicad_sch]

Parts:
C1, C4, C23, C27, C33, C35, C41: 4.7uF; C_0402_1005Metric; LCSC C23733
C2, C11, C17, C18, C19, C24, C25, C28, C30, C31, C36: 0.1uF; C_0402_1005Metric
C3, C6, C7, C16, C20: 0.1uF/35V; C_0603_1608Metric; LCSC C14663
C5: 22nf/50V; C_0603_1608Metric; LCSC C21122
C8: 100uF/35V; CP_Elec_6.3x5.8; LCSC C249982
C9, C10, C34, C42: 0.1uF; C_0402_1005Metric; LCSC C1525
C12, C26, C29: 22pF; C_0402_1005Metric; LCSC C1555
C13: 22pF; C_0402_1005Metric
C14, C15, C32: 22uF; C_0805_2012Metric; LCSC C45783
C21: 68pF; C_0402_1005Metric; LCSC C14441
C22: 10uF/35V; C_1210_3225Metric; LCSC C13585
C37, C38, C39, C40: 470pF/100V; C_0603_1608Metric; LCSC C107062
D1, D2, D3, D5: LEDGR; LED_0402_1005Metric; LCSC C74338
D6, D8: LEDRED; LED_0603_1608Metric; LCSC C2286
D7: SM24CANB; SOT-23; LCSC C970029
GND2: TestPoint; TestPoint_Pad_D1.0mm
H1, H2, H3, H4: MountingHole; MountingHole_3.2mm_M3_Pad_Via
J1: Conn_02x02_Odd_Even; Molex_Micro-Fit_3.0_43045-0400_2x02_P3.00mm_Horizontal; LCSC C122413
J2: DBG; PinHeader_2x03_P2.54mm_Vertical; LCSC C65114
J3: THERM; JST_PH_B3B-PH-K_1x03_P2.00mm_Vertical; LCSC C2320
J4: FAN0; JST_PH_B2B-PH-K_1x02_P2.00mm_Vertical; LCSC C2319
J5: FAN1; JST_PH_B2B-PH-K_1x02_P2.00mm_Vertical; LCSC C2319
J6: Heater; TerminalBlock_TE_282834-2_1x02_P2.54mm_Horizontal; LCSC C557685
J7: Endstop; JST_PH_B5B-PH-K_1x05_P2.00mm_Vertical; LCSC C2322
J9: STEPPER; JST_XH_B4B-XH-A_1x04_P2.50mm_Vertical; LCSC C144395
J12: USB_Micro-B_Molex-105017-0001; LCSC C10418
JP1, JP2: Jumper_3_Bridged12; SolderJumper-3_P1.3mm_Bridged12_Pad1.0x1.5mm
JP3: Jumper; PinHeader_1x02_P2.00mm_Vertical; LCSC C376075
L1: 22uH; L_0805_2012Metric; LCSC C32375
L4: 10uH/max 145mOhm 2A; L_Sunlord_MWSA0518_5.4x5.2mm; LCSC C408412
LOGO1: Logo_Open_Hardware_Small; OSHW-Symbol_6.7x6mm_SilkScreen
NT1: Net-Tie_2; NetTie-2_SMD_Pad0.5mm
Q1, Q2: AO3400A; SOT-23; LCSC C20917
Q3: AON7524; DFN-8-1EP_3x3mm_P0.65mm_EP1.7x2.05mm; LCSC C431195
R1, R5, R8, R10, R12, R13, R14, R15, R21, R23, R30: 10k; R_0402_1005Metric; LCSC C25744
R2, R31: 2.2k 0.1%; R_0402_1005Metric; LCSC C445604
R3, R20: 470; R_0402_1005Metric; LCSC C25117
R4, R7: 0.110 1%; R_1206_3216Metric
R6: 1k; R_0402_1005Metric; LCSC C11702
R9: 1M; R_0402_1005Metric; LCSC C26083
R11, R19, R22, R32, R33, R36, R37, R42, R43: 10k; R_0402_1005Metric
R16: 1k; R_0402_1005Metric; LCSC C21190
R17, R18, R24, R39: 22k; R_0402_1005Metric; LCSC C25768
R25, R34: 22; R_0402_1005Metric; LCSC C25092
R26, R28, R35: 22; R_0402_1005Metric
R27, R29: 2.2k; R_0402_1005Metric; LCSC C25879
R38: 120 100mW; R_0603_1608Metric; LCSC C22787
R40: 100k; R_0402_1005Metric; LCSC C25741
R41: 13.7k; R_0402_1005Metric; LCSC C25854
TP1, TP6: TestPoint; TestPoint_Pad_D1.0mm
U1: ADXL345; LGA-14_3x5mm_P0.8mm_LayoutBorder1x6y; LCSC C9667
U2: TMC2209-LA; LCSC C465949
U3: TPS54202; SOT-23-6; LCSC C191884
U4: XC6206PxxxMR; SOT-23; LCSC C5446
U5: STM32F103C8T6; LQFP-48_7x7mm_P0.5mm; LCSC C8734
U6: SN65HVD230; SOIC-8_3.9x4.9mm_P1.27mm; LCSC C12084
VIN1: TestPoint; TestPoint_Pad_D1.0mm
Y1: 8Mhz; Crystal_SMD_5032-2Pin_5.0x3.2mm; LCSC C115962

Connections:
+3V3: C1.1, C9.2, C10.1, C17.1, C18.1, C24.1, C27.1, C28.2, C33.2, C34.2, D5.2 (A), D8.2 (A), J2.2, L1.1, R1.1, R18.1, R19.2, R27.2, R32.1, R39.2, R42.2, TP6.1, U1.1 (Vdd_I/O), U2.15 (VCC_IO), U4.2 (VO), U5.1 (VBAT), U5.24 (VDD), U5.36 (VDD), U5.48 (VDD), U6.3 (VCC)
+5V: C14.1, C15.1, C32.1, C35.2, J7.5, L4.2, R29.2, R40.2, U4.3 (VI)
ACS: U1.7 (~CS), U5.19 (PB1)
AINT1: U1.8 (INT1), U5.18 (PB0)
AREF: C11.2, C23.2, C41.2, C42.2, L1.2, R2.2, R31.2, U1.6 (Vs), U5.9 (VDDA)
ASCL: U1.14 (SCL/SCLK), U5.26 (PB13)
ASDI: U1.13 (SDA/SDI/SDIO), U5.28 (PB15)
ASDO: U1.12 (SDO/ADDR), U5.27 (PB14)
BOOT0: R23.2, TP1.1, U5.44 (BOOT0)
BOOT1: J2.1, R37.2, U5.20 (PB2)
BRA: R4.2, U2.23 (BRA)
BRB: R7.2, U2.27 (BRB)
CANH: C29.2, D7.1 (K), JP2.1 (A), R38.1, U6.7 (CANH)
CANL: C26.1, D7.2 (K), JP1.1 (A), JP3.2, U6.6 (CANL)
CANRX: U5.45 (PB8), U6.4 (R)
CANTX: U5.46 (PB9), U6.1 (D)
DM: J12.2 (D-), JP1.3 (B), R26.2
DP: J12.3 (D+), JP2.3 (B), R25.2
ENDSTOP1: C30.1, R33.2, U5.21 (PB10)
ENDSTOP2: C31.1, R43.2, U5.22 (PB11)
ENDSTOP3: C2.1, R36.2, U5.25 (PB12)
FAN0: R8.2, R34.1, U5.29 (PA8)
FAN1: R10.2, R35.1, U5.17 (PA7)
GND: C1.2, C2.2, C4.2, C6.2, C7.2, C8.2, C9.1, C10.2, C12.1, C13.1, C14.2, C15.2, C16.2, C17.2, C18.2, C19.1, C22.1, C24.2, C26.2, C27.2, C28.1, C29.1, C30.2, C31.2, C32.2, C33.1, C34.1, C35.1, C37.1, C38.1, C39.1, C40.1, C41.1, C42.1, D7.3 (A), GND2.1, H1.1, H2.1, H3.1, H4.1, J1.3, J2.4, J7.4, J12.4 (ID), J12.5 (GND), NT1.1, Q1.2 (S), Q2.2 (S), Q3.1 (S), R4.1, R6.2, R7.1, R8.1, R10.1, R11.2, R12.1, R17.2, R20.2, R21.1, R22.2, R23.1, R24.1, R37.1, R41.1, U1.2 (GND), U1.4 (GND), U1.5 (GND), U2.3 (GND), U2.7 (SPREAD), U2.9 (MS1_AD0), U2.10 (MS2_AD1), U2.18 (GND), U2.20 (STDBY), U2.29 (EPAD), U3.1 (GND), U4.1 (GND), U5.23 (VSS), U5.35 (VSS), U5.47 (VSS), U6.2 (GND)
GNDA: C11.1, C23.1, C25.1, C36.1, J3.1, NT1.2, U5.8 (VSSA)
HEATER: R12.2, R28.1, U5.16 (PA6)
LED0: R3.1, U5.2 (PC13)
NRST: C19.2, J2.3, R1.2, U5.7 (NRST)
unnamed: C3.1, U2.6 (VCP)
unnamed: C4.1, U2.8 (5VOUT)
unnamed: C5.1, U2.5 (CPI)
unnamed: C5.2, U2.4 (CPO)
unnamed: C12.2, R9.1, U5.6 (PD1), Y1.1
unnamed: C13.2, R9.2, U5.5 (PD0), Y1.2
unnamed: C20.1, L4.1, U3.2 (SW)
unnamed: C20.2, U3.6 (BOOT)
unnamed: C21.1, R40.1, R41.2, U3.4 (FB)
unnamed: C21.2, R29.1
unnamed: D1.1 (K), J4.2, Q1.3 (D)
unnamed: D1.2 (A), R13.2
unnamed: D2.1 (K), J5.2, Q2.3 (D)
unnamed: D2.2 (A), R14.2
unnamed: D3.1 (K), J6.2, Q3.3 (D)
unnamed: D3.2 (A), R15.2
unnamed: D5.1 (K), R3.2
unnamed: D6.1 (K), R11.1
unnamed: D8.1 (K), R20.1
unnamed: J1.1, JP1.2 (C)
unnamed: J3.2, R2.1, R5.2
unnamed: J3.3, R30.2, R31.1
unnamed: J7.1, R32.2, R33.1
unnamed: J7.2, R42.1, R43.1
unnamed: J7.3, R19.1, R36.1
unnamed: J1.2, JP2.2 (C)
unnamed: JP3.1, R38.2
unnamed: Q1.1 (G), R34.2
unnamed: Q2.1 (G), R35.2
unnamed: Q3.2 (G), R28.2
unnamed: R6.1, U6.8 (Rs)
unnamed: R17.1, U2.13 (CLK)
ST_A1: C37.2, J9.2, U2.24 (OA1)
ST_A2: C38.2, J9.1, U2.21 (OA2)
ST_B1: C39.2, J9.3, U2.26 (OB1)
ST_B2: C40.2, J9.4, U2.1 (OB2)
ST_DIAG: R39.1, U2.11 (DIAG), U5.38 (PA15)
ST_DIR: U2.19 (DIR), U5.40 (PB4)
ST_EN: R18.2, U2.2 (ENN), U5.41 (PB5)
ST_STEP: U2.16 (STEP), U5.39 (PB3)
ST_UART_RX: R16.2, R24.2, U2.14 (PDN_UART), U5.31 (PA10)
ST_UART_TX: R16.1, U5.30 (PA9)
ST_VS: C3.2, C6.1, C7.1, C8.1, C16.1, C22.2, D6.2 (A), J1.4, J4.1, J5.1, J6.1, R13.1, R14.1, R15.1, U2.22 (VS), U2.28 (VS), U3.3 (VIN), VIN1.1
SWCLK: J2.6, R21.2, U5.37 (PA14)
SWDIO: J2.5, R22.1, U5.34 (PA13)
THERM: C25.2, R5.1, U5.10 (PA0)
THERM2: C36.2, R30.1, U5.11 (PA1)
USBDM: R26.1, U5.32 (PA11)
USBDP: R25.1, R27.1, U5.33 (PA12)

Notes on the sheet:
3.3V
5V Regulator
TODO:
Debug
0.62
Alt: RU3040M2 LN8342DT1AG JSM7788
Thermistor
Heater and fans mosfets
*** Features *** More spare general pins
CAN Tranciever
Alt: TPS54308 TPS54302
**Tweaks** Choke on CANL/CANH

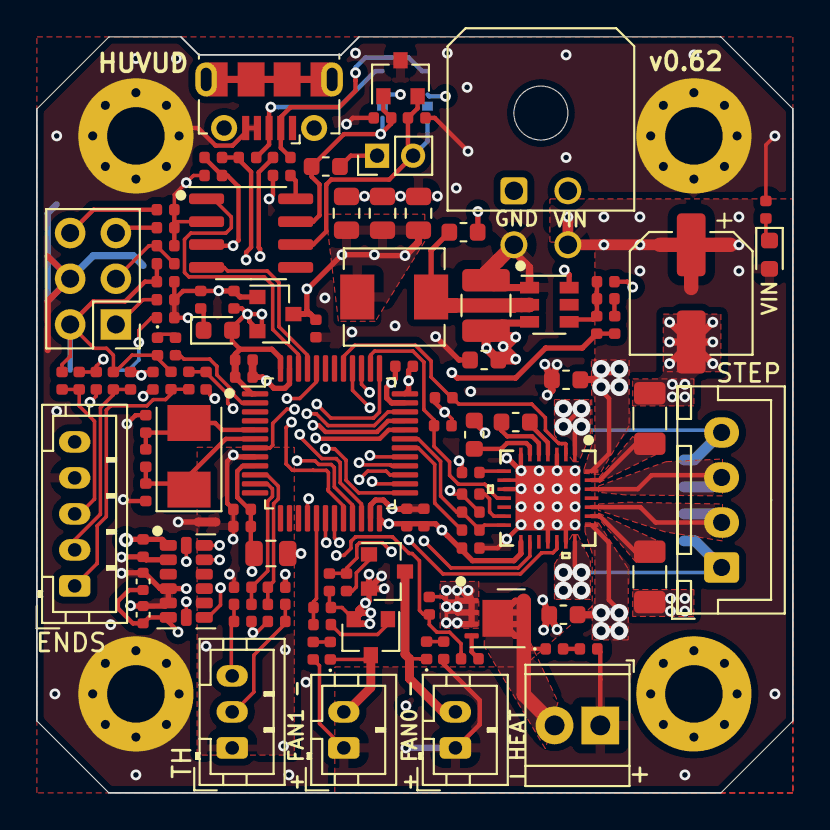
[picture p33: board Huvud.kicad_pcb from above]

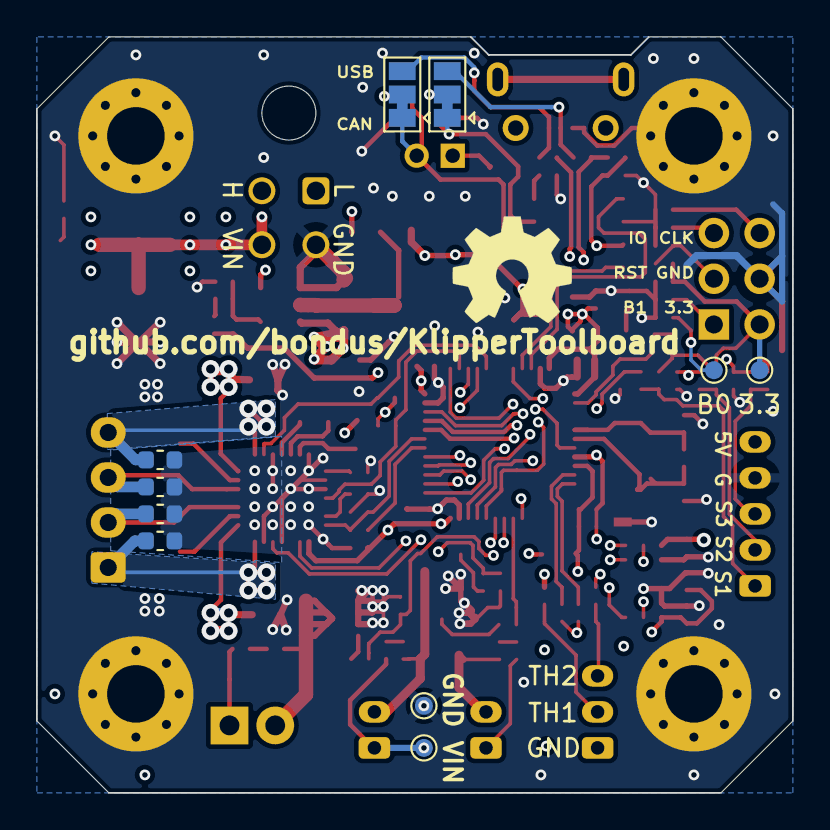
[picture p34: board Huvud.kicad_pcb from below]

Board: 4 copper layers, 42.0 x 42.0 mm, 126 parts (11 on the bottom side), 77 nets.

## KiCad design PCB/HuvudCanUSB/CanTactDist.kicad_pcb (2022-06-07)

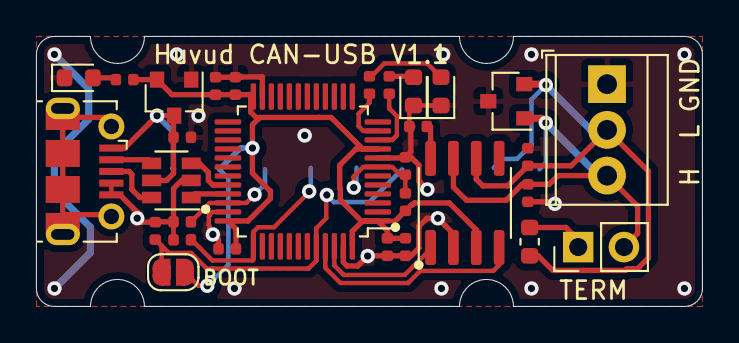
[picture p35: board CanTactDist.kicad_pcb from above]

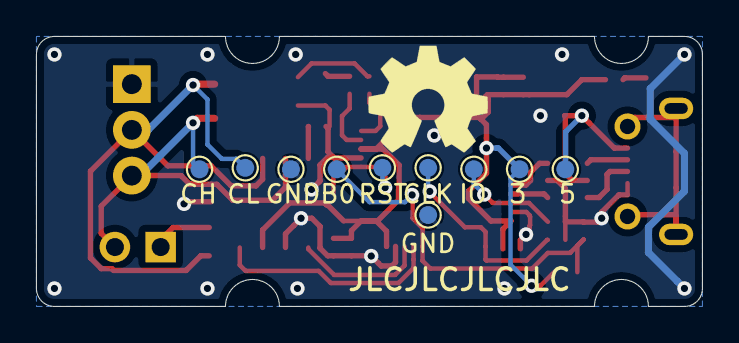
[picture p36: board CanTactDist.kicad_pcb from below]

Board: 2 copper layers, 37.0 x 15.0 mm, 41 parts (11 on the bottom side), 22 nets.

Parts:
BOOT0: TestPoint; TestPoint_Pad_D1.0mm
C2, C3: 4.7uF; C_0402_1005Metric
C10, C17, C18, C19, C28: 0.1uF; C_0402_1005Metric
C26, C29: 22pF; C_0402_1005Metric
CANH1: TestPoint; TestPoint_Pad_D1.0mm
CANL1: TestPoint; TestPoint_Pad_D1.0mm
D1, D5: LEDGR; LED_0603_1608Metric
D2: SMC24CANB; SOT-23
D8: LEDRED; LED_0603_1608Metric
GND1, GND3: TestPoint; TestPoint_Pad_D1.0mm
J1: Conn_01x03; TerminalBlock_TE_282834-3_1x03_P2.54mm_Horizontal
J4: Conn_01x02; PinHeader_1x02_P2.54mm_Vertical
J12: USB_Micro-B_Molex-105017-0001
LOGO1: Logo_Open_Hardware_Small; OSHW-Symbol_6.7x6mm_SilkScreen
NRST1: TestPoint; TestPoint_Pad_D1.0mm
R1, R21, R22, R23: 10k; R_0402_1005Metric
R2, R3, R20: 2.2k; R_0402_1005Metric
R4: 120; R_0603_1608Metric
R6: 1k; R_0402_1005Metric
SWCLK1: TestPoint; TestPoint_Pad_D1.0mm
SWIO1: TestPoint; TestPoint_Pad_D1.0mm
TP1: TestPoint_2Pole; SolderJumper-2_P1.3mm_Open_RoundedPad1.0x1.5mm
U1: STM32F042C6Tx; LQFP-48_7x7mm_P0.5mm
U2: XC6206P332MR; SOT-23
U3: USBLC6-2SC6; SOT-23-6
U6: SN65HVD230; SOIC-8_3.9x4.9mm_P1.27mm
V5, V33: TestPoint; TestPoint_Pad_D1.0mm

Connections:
+3V3: C3.2, C10.1, C17.1, C18.1, C28.2, R1.1, R20.1, TP1.2, U1.1, U1.9, U1.24, U1.36, U1.48, U2.2, U6.3, V33.1
+5V: C2.2, J12.1, U2.3, U3.5, V5.1
BOOT0: BOOT0.1, R23.2, TP1.1, U1.44
CANH: C29.2, CANH1.1, D2.1, J1.3, J4.2, U6.7
CANL: C26.1, CANL1.1, D2.2, J1.2, R4.2, U6.6
CANRX: U1.45, U6.4
CANTX: U1.46, U6.1
DM: J12.2, U3.4
DP: J12.3, U3.6
GND: C2.1, C3.1, C10.2, C17.2, C18.2, C19.1, C26.2, C28.1, C29.1, D1.1, D2.3, D5.1, D8.1, GND1.1, GND3.1, J1.1, J12.4, J12.5, R6.2, R21.2, R22.2, R23.1, U1.8, U1.23, U1.35, U1.47, U2.1, U3.2, U6.2
LED0: R3.1, U1.10
LED1: R2.1, U1.11
NRST: C19.2, NRST1.1, R1.2, U1.7
unnamed: D1.2, R2.2
unnamed: D5.2, R3.2
unnamed: D8.2, R20.2
unnamed: J4.1, R4.1
unnamed: R6.1, U6.8
SWCLK: R21.1, SWCLK1.1, U1.37
SWDIO: R22.1, SWIO1.1, U1.34
USBDM: U1.32, U3.3
USBDP: U1.33, U3.1

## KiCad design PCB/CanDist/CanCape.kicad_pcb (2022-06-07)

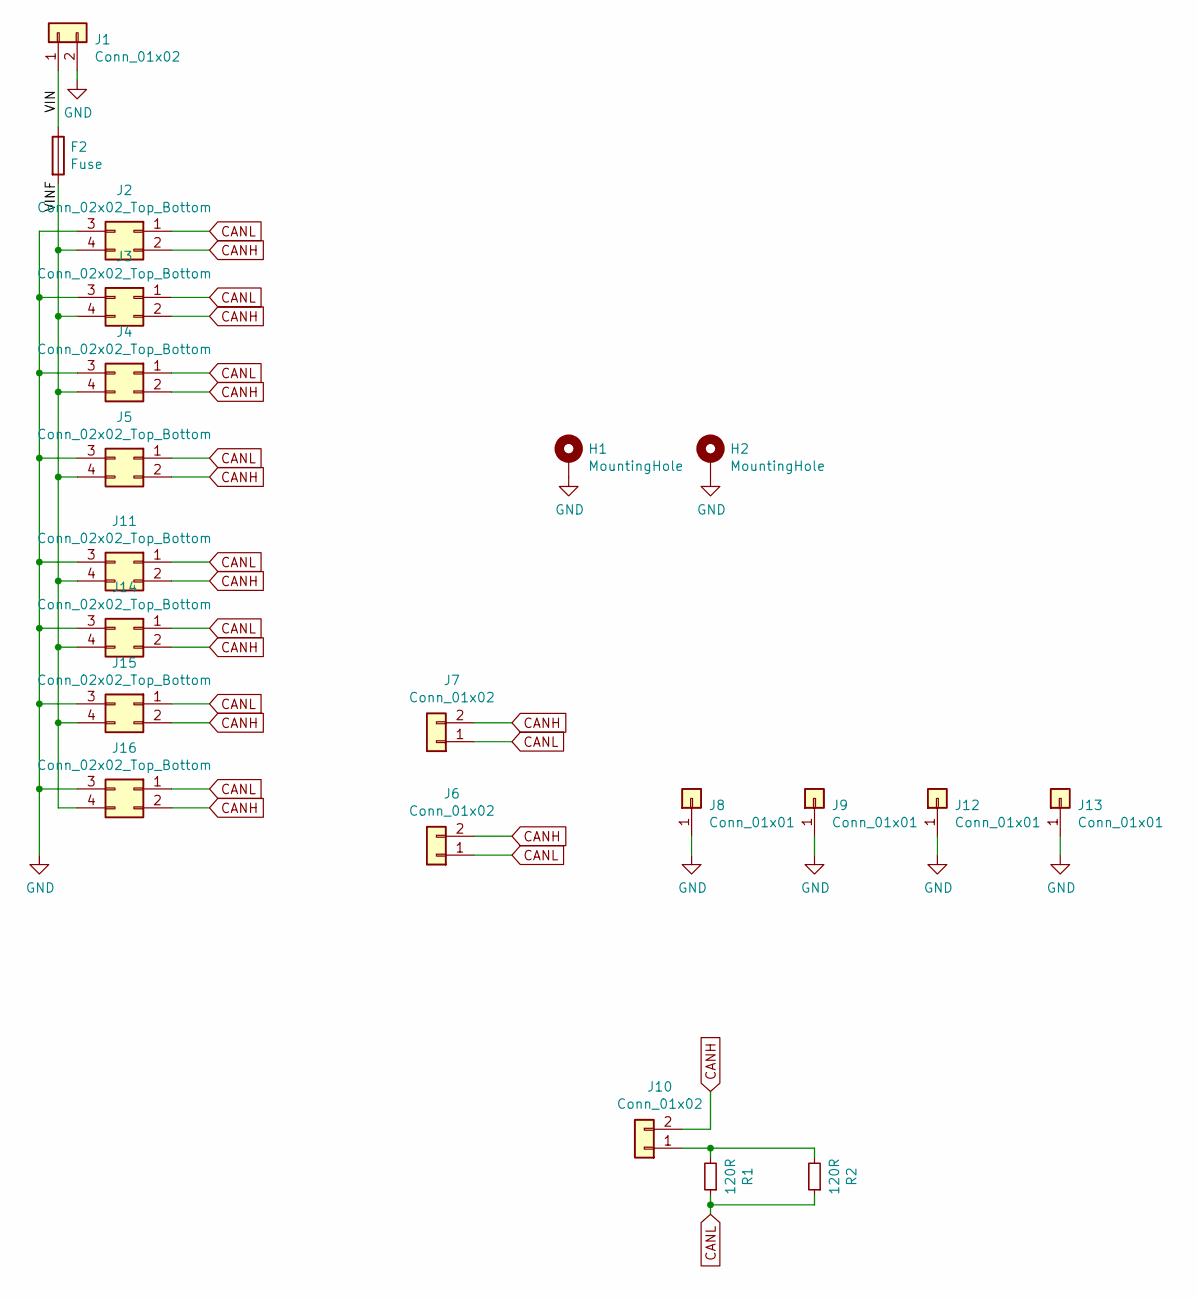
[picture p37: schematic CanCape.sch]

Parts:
F2: Fuse; KEYSTONE-3568
H1, H2: MountingHole; MountingHole_3.2mm_M3_Pad_Via
J1: Conn_01x02; TerminalBlock_bornier-2_P5.08mm
J2, J3, J4, J5: Conn_02x02_Top_Bottom; Molex_Micro-Fit_3.0_43045-0412_2x02_P3.00mm_Vertical
J6, J7: Conn_01x02; JST_XH_B2B-XH-A_1x02_P2.50mm_Vertical
J8, J9, J12, J13: Conn_01x01; PinHeader_1x01_P2.54mm_Vertical
J10: Conn_01x02; PinHeader_1x02_P2.54mm_Vertical
J11, J14, J15, J16: Conn_02x02_Top_Bottom; Molex_Micro-Fit_3.0_43045-0400_2x02_P3.00mm_Horizontal
R1: 120R; R_0603_1608Metric; LCSC Part # C22787
R2: 120R; R_Axial_DIN0207_L6.3mm_D2.5mm_P7.62mm_Horizontal

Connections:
/VIN: F2.1, J1.1
/VINF: F2.2, J2.4, J3.4, J4.4, J5.4, J11.4, J14.4, J15.4, J16.4
CANH: J2.2, J3.2, J4.2, J5.2, J6.2, J7.2, J10.2, J11.2, J14.2, J15.2, J16.2
CANL: J2.1, J3.1, J4.1, J5.1, J6.1, J7.1, J11.1, J14.1, J15.1, J16.1, R1.1, R2.1
GND: H1.1, H2.1, J1.2, J2.3, J3.3, J4.3, J5.3, J8.1, J9.1, J11.3, J12.1, J13.1, J14.3, J15.3, J16.3
unnamed: J10.1, R1.2, R2.2

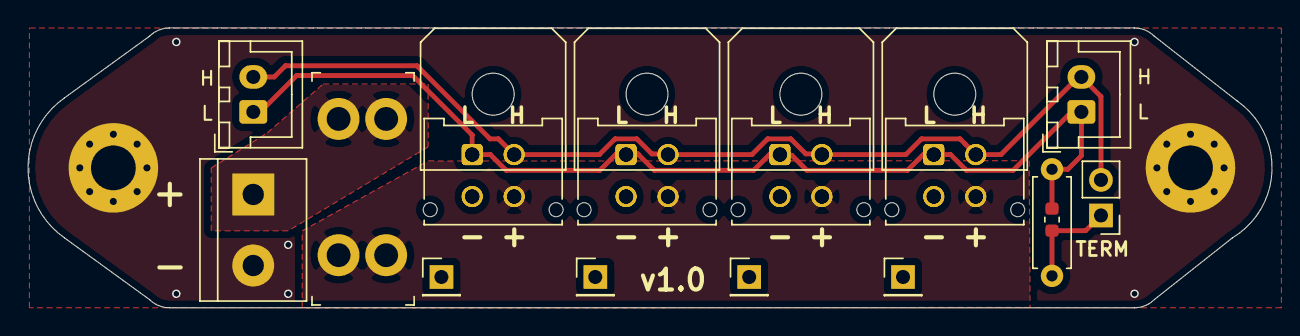
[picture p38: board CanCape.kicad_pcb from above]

Board: 2 copper layers, 88.9 x 20.0 mm, 21 parts (0 on the bottom side), 6 nets.

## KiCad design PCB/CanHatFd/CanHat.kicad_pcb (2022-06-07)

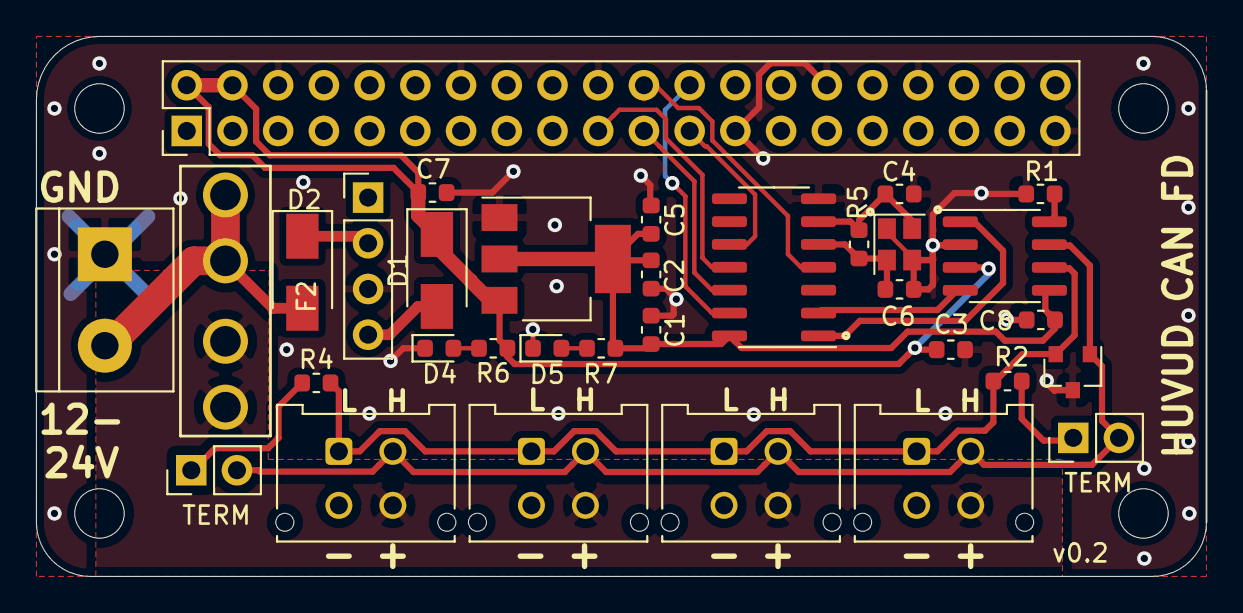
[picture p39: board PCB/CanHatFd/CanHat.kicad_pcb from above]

Board: 2 copper layers, 65.0 x 30.0 mm, 33 parts (0 on the bottom side), 23 nets.

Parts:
C1, C2, C3, C8: 100nF; C_0603_1608Metric
C4, C6: 15pF; C_0603_1608Metric
C5, C7: 4.7uF; C_0603_1608Metric
D1, D2: SS34; D_SMA
D3: SM24CANB; SOT-23
D4, D5: LED; LED_0603_1608Metric
F2: Fuse; 3544-2_FuseHolder
J1: Raspberry_Pi_2_3; PinHeader_2x20_P2.54mm_Vertical
J2: Conn_01x02; TerminalBlock_bornier-2_P5.08mm
J3, J4, J5, J6: Conn_02x02_Top_Bottom; Molex_Micro-Fit_3.0_43045-0412_2x02_P3.00mm_Vertical
J7, J8: Conn_01x02; PinHeader_1x02_P2.54mm_Vertical
J15: Conn_01x04; DCDRegulator
R1: 470R; R_0603_1608Metric
R2, R4: 120R; R_0603_1608Metric
R5: 1M; R_0603_1608Metric
R6: 2.2k; R_0603_1608Metric
R7: 1k; R_0603_1608Metric
U1: MCP2517FD-xSL; SOIC-14_3.9x8.7mm_P1.27mm
U2: AP1117-33; SOT-223-3_TabPin2
U4: MCP2562-E-SN; SOIC-8_3.9x4.9mm_P1.27mm
Y1: Crystal_GND24; Crystal_SMD_2520-4Pin_2.5x2.0mm

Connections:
5VPI: C3.1, C7.1, D1.1, J1.2, J1.4, R6.2, U2.3, U4.3
+3V3: C1.2, C2.1, C5.1, C8.2, R7.2, U1.14, U2.2, U4.5
/RX: U1.2, U4.4
/TX: U1.1, U4.1
CANH: D3.1, J3.2, J4.2, J5.2, J6.2, J7.2, J8.2, U4.7
CANL: D3.2, J3.1, J4.1, J5.1, J6.1, R2.1, R4.1, U4.6
GND: C1.1, C2.2, C3.2, C4.1, C5.2, C6.1, C7.2, C8.1, D3.3, D4.1, D5.1, J1.6, J1.9, J1.14, J1.20, J1.25, J1.30, J1.34, J1.39, J2.1, J3.3, J4.3, J5.3, J6.3, J15.3, R1.1, U1.7, U2.1, U4.2, Y1.1, Y1.3
GPIO25: J1.22, U1.4
MISO: J1.21, U1.12
MOSI: J1.19, U1.11
unnamed: C4.2, R5.1, U1.6, Y1.4
unnamed: C6.2, R5.2, U1.5, Y1.2
unnamed: D1.2, J15.4
unnamed: D2.2, F2.1, J2.2
unnamed: D4.2, R6.1
unnamed: D5.2, R7.1
unnamed: J7.1, R4.2
unnamed: J8.1, R2.2
unnamed: R1.2, U4.8
SCK: J1.23, U1.10
VDC: D2.1, J15.2
VOUT: F2.2, J3.4, J4.4, J5.4, J6.4
nCS: J1.24, U1.13

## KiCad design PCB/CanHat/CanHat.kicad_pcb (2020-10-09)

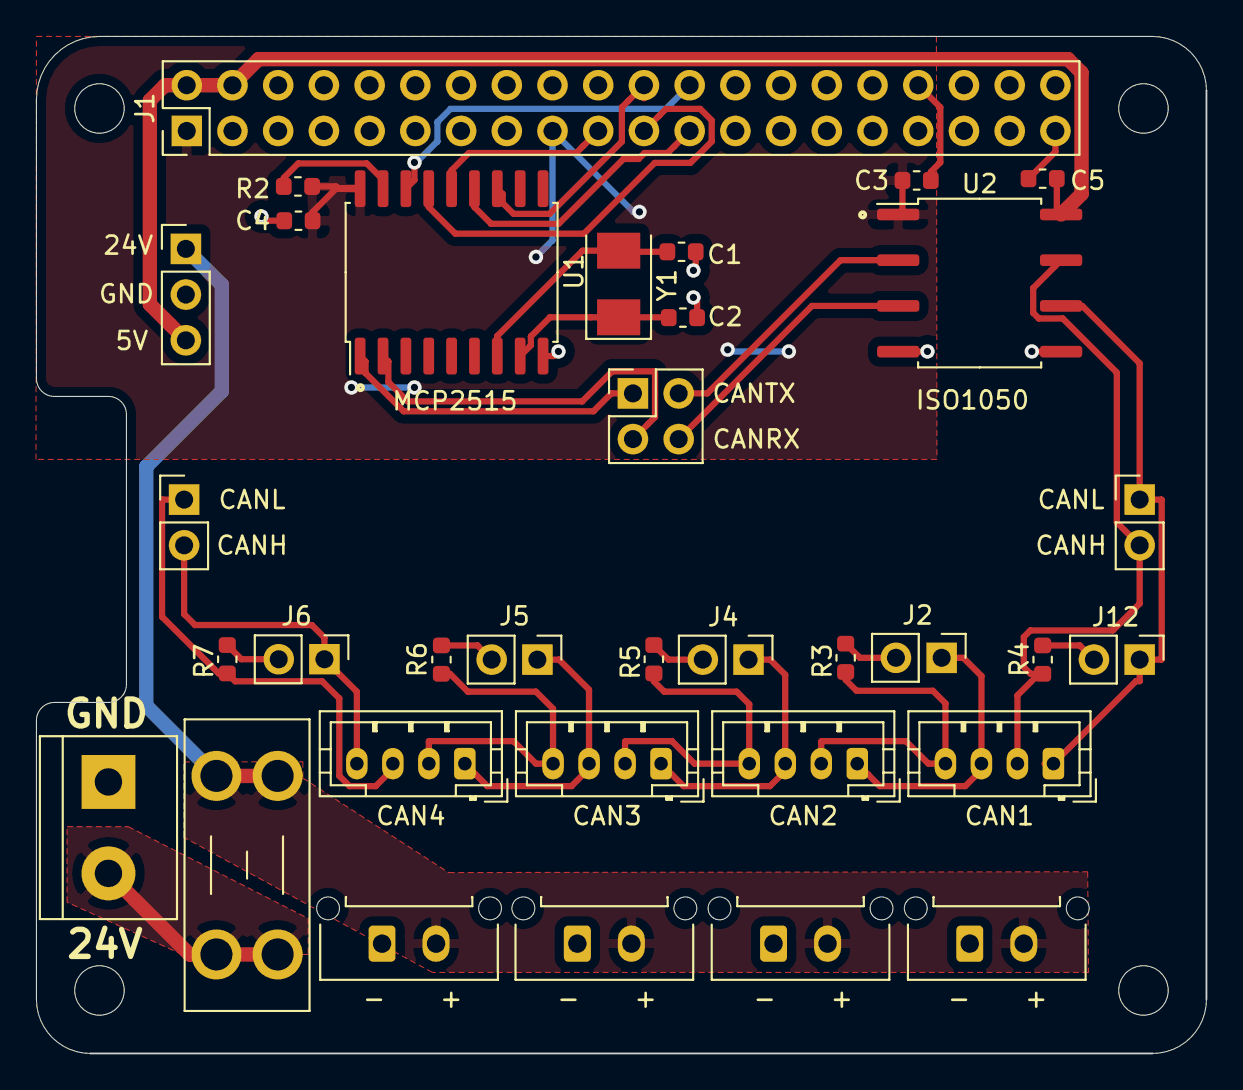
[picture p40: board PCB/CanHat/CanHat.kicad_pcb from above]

Board: 2 copper layers, 65.0 x 56.5 mm, 34 parts (0 on the bottom side), 32 nets.

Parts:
C1, C2: 22p; C_0603_1608Metric
C3, C4, C5: 0.1uF; C_0603_1608Metric
CAN1, CAN2, CAN3, CAN4: Conn_01x04; JST_PH_B4B-PH-K_1x04_P2.00mm_Vertical
F1: Fuse; Fuseholder_Blade_Mini_Keystone_3568
J1: Raspberry_Pi_2_3; PinHeader_2x20_P2.54mm_Vertical
J2, J4, J5, J6, J12, J13, J14: Conn_01x02; PinHeader_1x02_P2.54mm_Vertical
J3: Conn_01x02; TerminalBlock_bornier-2_P5.08mm
J7, J8, J9, J10: Conn_01x02; Molex_Micro-Fit_3.0_43650-0215_1x02_P3.00mm_Vertical
J11: Conn_02x02_Odd_Even; PinHeader_2x02_P2.54mm_Vertical
J15: Conn_01x04; PinHeader_1x03_P2.54mm_Vertical
R2: 10k; R_0603_1608Metric
R3, R4, R5, R6, R7: 120R; R_0603_1608Metric
U1: MCP2515-xSO; SOIC-18W_7.5x11.6mm_P1.27mm
U2: ISO1050DUB; SOP-8_6.62x9.15mm_P2.54mm
Y1: Crystal; Crystal_SMD_5032-2Pin_5.0x3.2mm

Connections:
+3V3: C3.2, C4.2, J1.1, J1.17, R2.2, U1.18, U2.1
+5V: C5.2, J1.2, J1.4, J15.3, U2.8
/CANRX: J11.4, U2.3
/CANTX: J11.2, U2.2
CANH: CAN1.2, J13.2, R4.1, U2.7
CANL: CAN1.1, J12.1, J13.1, U2.6
CS: J1.24, U1.16
GND: C1.2, C2.2, C3.1, C4.1, C5.1, J1.6, J1.9, J1.14, J1.20, J1.25, J1.30, J1.34, J1.39, J3.1, J7.1, J8.1, J9.1, J10.1, J15.2, U1.9, U2.4, U2.5
GPIO25: J1.22, U1.12
MISO: J1.21, U1.15
MOSI: J1.19, U1.14
unnamed: C1.1, U1.7, Y1.2
unnamed: C2.1, U1.8, Y1.1
unnamed: CAN1.3, CAN2.1, J2.1
unnamed: CAN1.4, CAN2.2, R3.2
unnamed: CAN2.3, CAN3.1, J4.1
unnamed: CAN2.4, CAN3.2, R5.2
unnamed: CAN3.3, CAN4.1, J5.1
unnamed: CAN3.4, CAN4.2, R6.2
unnamed: CAN4.3, J14.1, R7.2
unnamed: CAN4.4, J6.1, J14.2
unnamed: F1.1, J3.2
unnamed: J2.2, R3.1
unnamed: J4.2, R5.1
unnamed: J5.2, R6.1
unnamed: J6.2, R7.1
unnamed: J11.1, U1.1
unnamed: J11.3, U1.2
unnamed: J12.2, R4.2
unnamed: R2.1, U1.17
SCK: J1.23, U1.13
VDC: F1.2, J7.2, J8.2, J9.2, J10.2, J15.1

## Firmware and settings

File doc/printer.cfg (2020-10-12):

# A partial printer.cfg for using the huvud control board
#
#

[mcu head0]
serial: /tmp/ttyCAN0_5aa658bb599a # Change to your ID
restart_method = command

[extruder]
step_pin: head0:PB3
dir_pin: head0:PB4
enable_pin: !head0:PB6
heater_pin: head0:PA6  # "HEAT"
step_distance: .002
nozzle_diameter: 0.400
filament_diameter: 1.750
sensor_type: EPCOS 100K B57560G104F
sensor_pin: head0:PA0 # "THERMISTOR"
pullup_resistor: 2200 # The board uses a 2.2k ohm pullup to work with a PT1000 
min_temp: 0
max_temp: 250

[tmc2209 extruder]
uart_pin: head0:PA10
tx_pin: head0:PA9
microsteps: 16
interpolate: True
run_current: 0.9
sense_resistor: 0.110
hold_current: 0.5
stealthchop_threshold: 0


[heater_fan extruder_fan]
pin: head0:PA8   # "FAN1"
heater: extruder
heater_temp: 50.0

[fan]
pin: head0:PA7  # "FAN0"


# endstop_pin = head0:PA1  "ENDSTOP", active low

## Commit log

2020-03-25 Initial version
    [JLCSMT_Sample_BOM1.xls, KlipperToolboard.kicad_pcb, KlipperToolboard.sch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]
2020-03-29 Changed to STM32
    [JLCSMT_Sample_BOM1.xls, KlipperToolboard.kicad_pcb, KlipperToolboard.sch]
2020-04-01 Change to STM32 and CAN Bus
    [KlipperToolboard.kicad_pcb, KlipperToolboard.sch]
2020-04-01 Updated board image
2020-04-02 3d models for JST ZH
    [B4B-ZR-3.4.STEP, B4B-ZR-SM4-TF.STEP, B4B-ZR.STEP]
2020-04-02 more 3d models
    [KlipperToolboard.kicad_pcb, Regulator.step, TE_282834-2--3DModel-STEP-56544.STEP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]
2020-04-02 Custom footprints
2020-04-02 Tweaks and 3d models
    [KlipperToolboard.kicad_pcb, KlipperToolboard.sch]
2020-05-18 Renamed to Huvud Changed to an STM32
    [B4B-ZR-3.4.STEP, B4B-ZR-SM4-TF.STEP, B4B-ZR.STEP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]
2020-05-18 Forgot some files
    [Huvud.kicad_pcb, Huvud.sch]
2020-05-18 Diodes by the connectors should be moved to allow for JST connectors be used for the fan connectors.
    [Huvud.kicad_pcb]
2020-05-18 TMC Heat notes
2020-05-18 Example partial printer.cfg
    [printer.cfg]
2020-05-28 Small steaks preparing for v0.4
    [Huvud.kicad_pcb, Huvud.sch, JLCSMT_Huvud_BOM1.xls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]
2020-05-28 More status updates and mentions of Can Hat
    [CanHat.sch]
2020-06-03 Working on 0.4 Thermistor contact moved along the power contacts(can/heater) Added a micro USB connector, useful for flashing Added an on board 3.3V regulator
    [CanHat.kicad_pcb, CanHat.sch, Huvud.kicad_pcb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]
2020-06-09 Tweaks to allow JST XH headers to fit fan outputs. PDF schematic
    [Huvud.kicad_pcb]
2020-06-20 BOM and POS or out of date
    [JLCSMT_Huvud_BOM1.xls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]
2020-06-24 Final (hopefully) tweaks to v0.4 before manufacture
    [Huvud-bom.csv, Huvud-bom.xls, Huvud.kicad_pcb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]
2020-06-26 Updated PDF schematics
2020-08-08 Update to v0.41
    [Huvud-bom.xls, Huvud.kicad_pcb, Huvud.sch]
2020-08-20 0.41 manufacturing files
    [Huvud_JLCPCB_bom.xls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]
2020-08-21 0.44 manufacture
    [Huvud - Copy.kicad_pcb, Huvud_JLCPCB_bom.xls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]
2020-08-22 Picture of 0.41 real board
2020-10-09 v0.44, v0.45
    [Huvud - Copy.kicad_pcb, Huvud.kicad_pcb, Huvud.sch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]
2020-10-09 schematics pdf
    [CanHat.kicad_pcb, CanHat.sch]
2020-10-12 Minor tweaks to the layout. Added some text on the back size
    [Huvud.kicad_pcb, Huvud.sch, printer.cfg]
2020-10-16 Added version of the board
2020-10-28 0.50 huvud
    [Huvud.kicad_pcb, Huvud.sch, Huvud_JLCPCB_bom.xls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]
2020-11-26 A small power and CAN distribution board. Work in progress
    [CanCape.kicad_pcb, CanCape.sch, file5F8EE623.sch]
2020-11-26 remove some junk
    [file5F8EE623.sch]
2021-01-05 A Pi CAN-fd hat with TMC2517
    [CanHat.kicad_pcb, CanHat.sch]
2021-01-05 Some footprints and gerbers for the CANfd hat
2021-02-16 A picture of the power and CAN distribution board
2021-03-04 Working on a Huvud board with 5V and an accelerometer. WIP!
    [Huvud.kicad_pcb, Huvud.sch]
2021-03-22 Work in progress.
    [B4B-ZR-3.4.STEP, B4B-ZR-SM4-TF.STEP, B4B-ZR.STEP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]
2021-05-04 Tweaks to Huvud 0.6x
    [Huvud.kicad_pcb, Huvud.sch]
2021-06-07 Step CAD file for Huvud 0.50
2021-07-24 Change to Huvud, v0.61 Added a second thermistor input Added pads for a CAN termination resistor on the back Added solder bridges to change the Molex connector from CAN to USB Changed some components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
    [Huvud.kicad_pcb, Huvud.sch]
2021-09-25 Assembly files for 0.61
    [Huvud_JLCPCB_bom.xls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]
2022-02-09 A small can/usb adapter for running candlelight firmware
    [48037-0001.step, CanTactDist.kicad_pcb, CanTactDist.sch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]
2022-02-19 Huvud 0.61 schematics pdf
2022-06-07 Added step file for Huvud v0.62
    [CanCape.kicad_pcb, CanCape.sch, CanHat.kicad_pcb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]
2022-08-01 Update to kicad 6
    [Huvud.kicad_pcb, Huvud.kicad_sch]
2022-09-26 Generated new gerbers and position files for Huvud 0.62
    [Huvud-B_Cu.gbr, Huvud-B_Mask.gbr, Huvud-B_Paste.gbr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]
2022-09-28 Updated BOM and POS files for JLCPCB. Q3,C14,C15 and C32 use different part numbers compared to the schematics. Most ICs are rotated wrong and have to be fixed by hand. There are markers on the silk 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
    [Huvud_JLCPCB_bom.xls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]

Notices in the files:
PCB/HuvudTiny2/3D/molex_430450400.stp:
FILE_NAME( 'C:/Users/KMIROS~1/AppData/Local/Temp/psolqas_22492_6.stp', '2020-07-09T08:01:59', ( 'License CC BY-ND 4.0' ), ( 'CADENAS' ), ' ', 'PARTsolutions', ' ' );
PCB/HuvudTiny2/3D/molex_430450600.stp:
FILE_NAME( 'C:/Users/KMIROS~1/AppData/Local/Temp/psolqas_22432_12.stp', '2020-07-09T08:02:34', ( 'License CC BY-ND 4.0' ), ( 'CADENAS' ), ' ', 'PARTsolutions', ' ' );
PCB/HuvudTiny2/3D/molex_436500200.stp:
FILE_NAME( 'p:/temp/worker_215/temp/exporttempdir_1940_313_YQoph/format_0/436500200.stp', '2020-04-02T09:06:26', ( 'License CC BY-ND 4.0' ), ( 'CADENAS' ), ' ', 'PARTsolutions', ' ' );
